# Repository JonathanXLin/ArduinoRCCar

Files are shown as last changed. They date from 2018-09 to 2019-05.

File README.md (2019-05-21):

# Wrist Controlled RC Car

This was a fun early project I made that let me consolidate my knowledge of C, Arduino electronics, and 3D modelling. I've included the Arduino code, prototype board schematics, and 3D models for the car and wrist controller.

<br>

<p align="center"> 
  
</p>

<p align="center"> 
  
</p>

<p align="center"> 
  
</p>

## Overview

The RC car uses two 12V geared DC motors, connected to a 2S Li-ion pack via a L293D dual H bridge. The H bridge is controlled by an Arduino Nano, which receives wireless commands from an NRF24L01 radio transceiver. 

The wrist controller consists of a GY-521 three-axis gyroscope module and an NRF24L01 radio transceiver controlled by an Arduino Nano. The controller is powered by a 9V battery.

<p align="center"> 
  
</p>

## Features

Once the car and wrist controller are powered on, the front lights will blink. When a connection is established (usually instant), the front lights will stay illuminated and the car will respond to the wrist controller. 

Holding the hand out parallel to the ground stops the car. Tilting the hand forward, back, left, and right drives the car in that respective direction. The car is capable of driving at a max forward speed of ~2 m/s, and can turn on a dime.

The car has a battery life of around 20 h of continuous heavy use.

## Code

All C code is original, except for the excellent TMRh20 library by Stefan Engelke for the NRF24L01 radio transceivers. 

## Schematics

The car and controller circuits were prototyped on breadboards before being built on two prototype boards. Fritzing was used to create digital schematics during this process.

## Models

The car shell and wheels were designed using SolidWorks and 3D printed using PLA filament. However, store bought wheels were used in the final design due to the need to superglue the 3D printed wheels (I might need to salvage the motors for later projects!)

## Photos

### Car Underside

<p align="center"> 
  
</p>

### Car and Controller Schematic Preview

<p align="center"> 
  
</p>

</br>

<p align="center"> 
  
</p>

### Prototypes

<p align="center"> 
  
</p>

</br>

<p align="center"> 
  
</p>

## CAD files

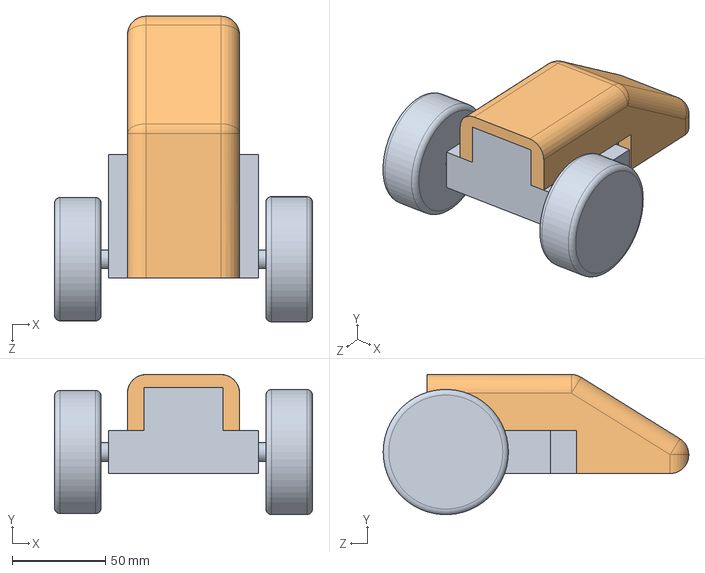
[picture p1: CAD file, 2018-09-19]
Models/V1 (Perfboard)/Car.SLDASM
138.0 x 74.9 x 163.5 mm
Internal Assembly

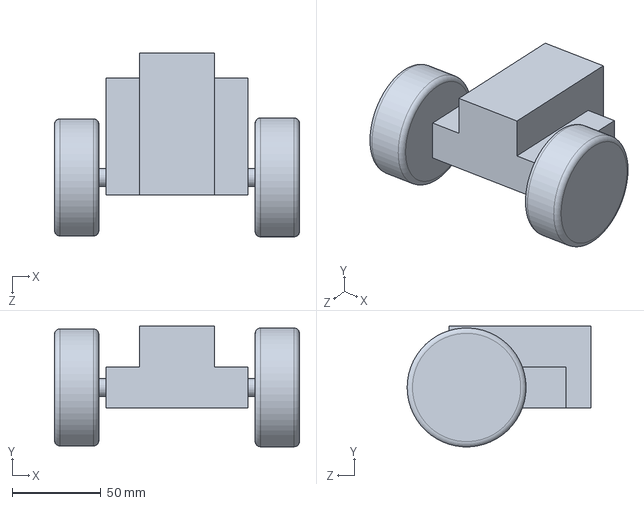
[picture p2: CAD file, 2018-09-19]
Models/V1 (Perfboard)/Internal Assembly.SLDPRT
138.0 x 67.9 x 103.5 mm

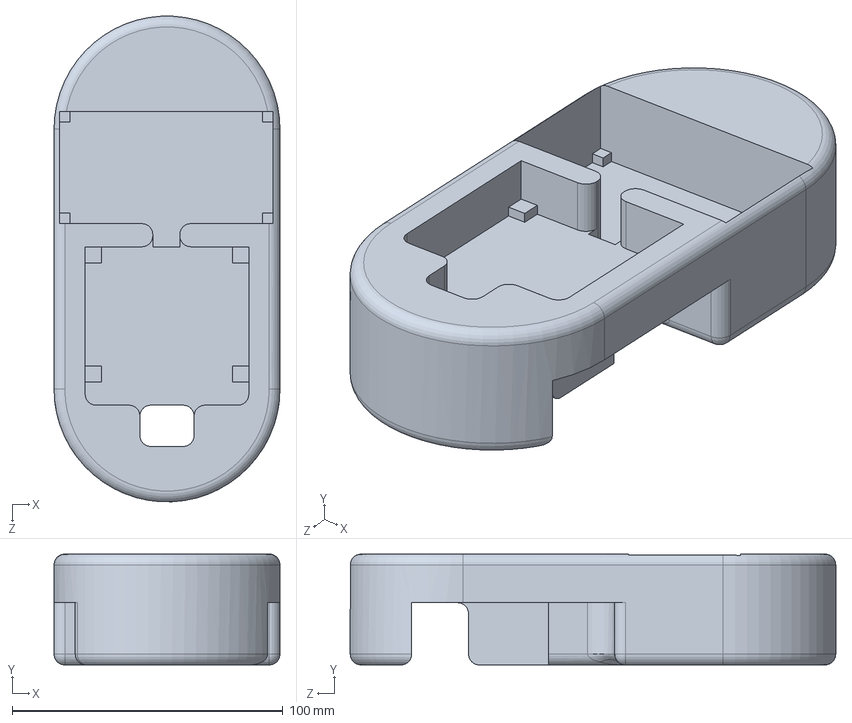
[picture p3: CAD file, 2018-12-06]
Models/V2 (PCB)/Car.SLDPRT
83.5 x 41.0 x 179.4 mm

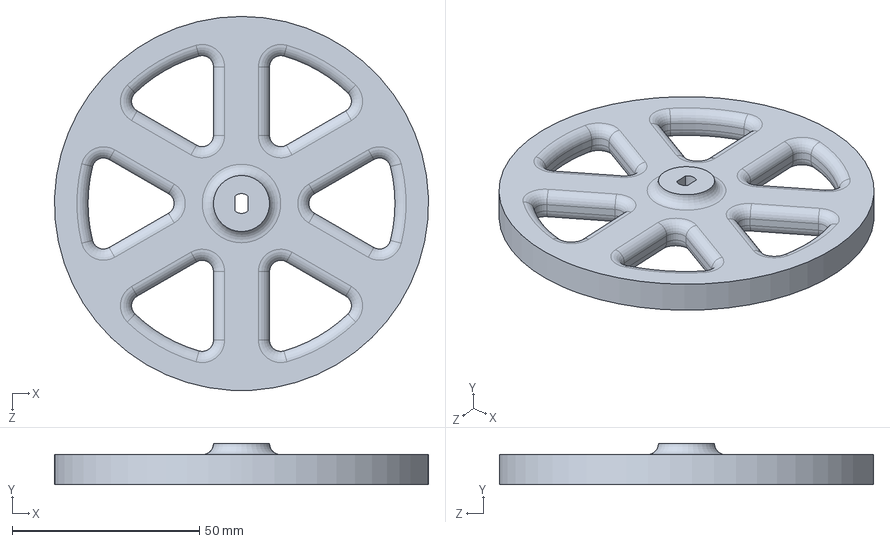
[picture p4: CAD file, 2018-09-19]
Models/V1 (Perfboard)/Traction Wheel.SLDPRT
100.0 x 11.0 x 100.0 mm

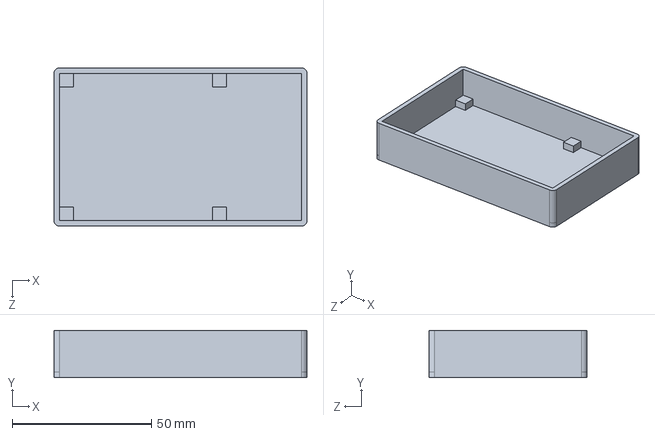
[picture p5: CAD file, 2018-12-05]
Models/V2 (PCB)/Controller (optional).SLDPRT
91.0 x 17.0 x 57.0 mm

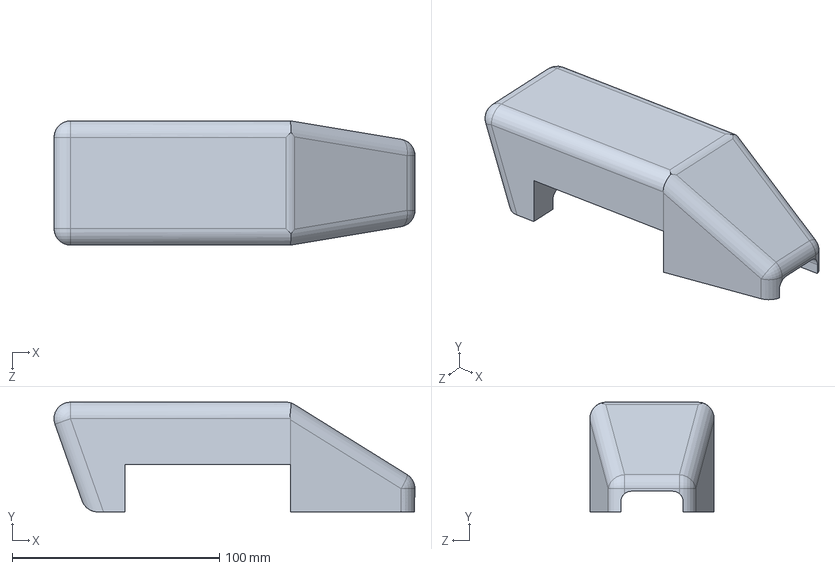
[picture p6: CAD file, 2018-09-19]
Models/V1 (Perfboard)/Shell.SLDPRT
174.2 x 53.0 x 60.0 mm

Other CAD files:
Models/V1 (Perfboard)/Shell.STL
Models/V2 (PCB)/Car.STL
Models/V2 (PCB)/Controller (optional).STL

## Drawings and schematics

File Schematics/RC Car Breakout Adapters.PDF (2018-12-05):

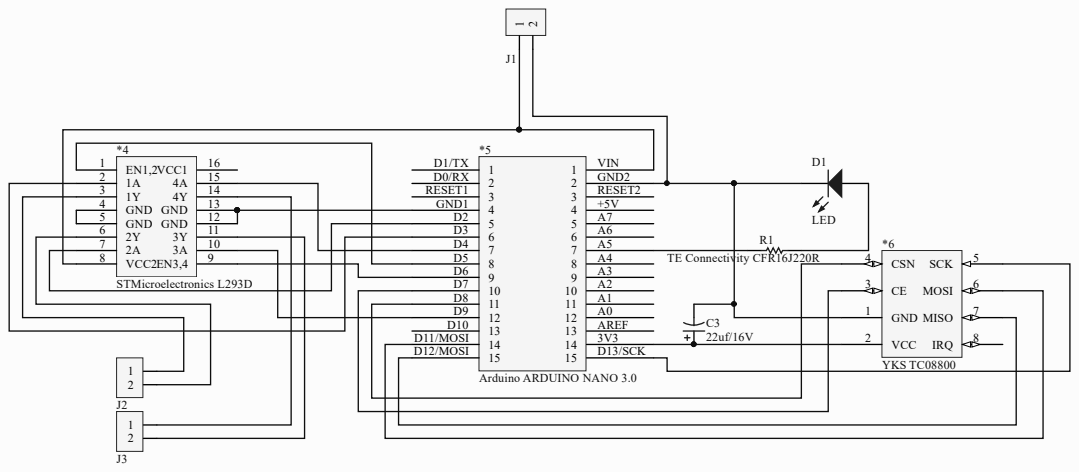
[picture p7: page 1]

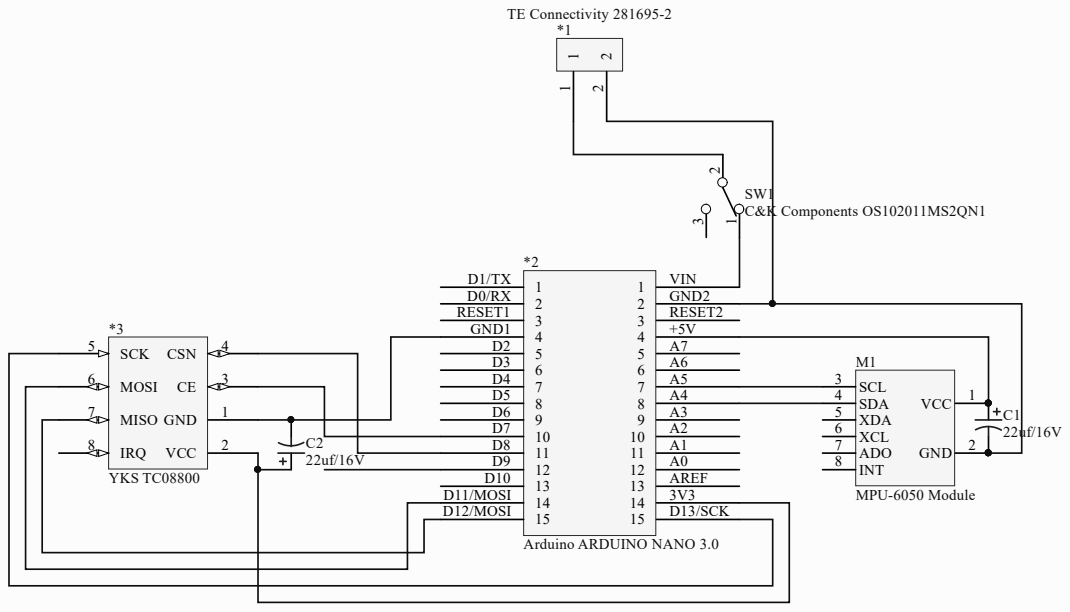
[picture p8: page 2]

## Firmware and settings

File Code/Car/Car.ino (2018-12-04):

#include <SPI.h>
#include "nRF24L01.h"
#include "RF24.h"

#include "Motor.h"

#define frontLED1   A5
#define frontLED2   A1

RF24 radio(7, 8);
//CE, CSN

const byte address[6] = "00001";

void setup() {
  
  radio.begin();
  radio.openReadingPipe(0, address);
  radio.setPALevel(RF24_PA_MAX);
  radio.setDataRate(RF24_250KBPS);
  radio.setChannel(115);
  radio.startListening();
  
  delay(200);

  Serial.begin(9600);
  Serial.println("Car Initialized");
  
  pinMode(ena, OUTPUT);
  pinMode(enb, OUTPUT);

  pinMode(in1, OUTPUT);
  pinMode(in2, OUTPUT);
  pinMode(in3, OUTPUT);
  pinMode(in4, OUTPUT);

  pinMode(frontLED1, OUTPUT);
  pinMode(frontLED2, OUTPUT);

  while (!radio.available())
  {
    front_light(150);
    delay(150);
  }

  front_light(1);
}

int ticksSinceLastConnection = 0;

int prevThrottle = 0;
int prevSteer = 0;

void loop() {

  read_and_drive();

  if (ticksSinceLastConnection >= 40)
  {
    prevThrottle = 0;
    prevSteer = 0;

    front_light(150);
    delay(150);
  }
  else
  {
    front_light(1);
  }

  delay(10);
}

bool isConnected = false;

void print_data()
{
  if (radio.available())
  {
    int package = -1;
    radio.read(&package, sizeof(int));
    
    int xState = package/100;
    int yState = package - xState*100;

    Serial.print("Package: ");
    Serial.print(package);
    Serial.print("\t");
    Serial.print("X: ");
    Serial.print(xState);
    Serial.print(" ");
    Serial.print("Y: ");
    Serial.print(yState);
    Serial.println();
  }
}

void read_data(int* xState, int* yState)
{
    int package = -1;
    radio.read(&package, sizeof(int));
    
    int x = package/100;
    int y = 0;
    
    if (x > 0)
      y = package - x*100 - 50;
    else
      y = package - x*100 + 50;

    if (x == 0)//Failed transmission, uses previous state
    {
      *xState = prevThrottle;
      *yState = prevSteer;

      ticksSinceLastConnection++;
    }
    else
    {
      if (x == 1)//Zero value transmitted
        *xState = 0;
      else//Nonzero value transmitted
        *xState = x;

      *yState = y*2;
        
      prevThrottle = *xState;
      prevSteer = *yState;

      Serial.print("Package: ");
      Serial.print(package);
      Serial.print("\t");
      Serial.print("X: ");
      Serial.print(*xState);
      Serial.print(" ");
      Serial.print("Y: ");
      Serial.print(*yState);
      Serial.println();

      ticksSinceLastConnection = 0;
    }
}

int xState = 0;
int yState = 0;

void read_and_drive()
{
  read_data(&xState, &yState);

  drive(xState + yState, xState - yState, 50);
}

void front_light(int dur)//if dur is 1, turns on, if dur is 0, turns off
{
  if (dur == 1)
  {
    digitalWrite(frontLED1, HIGH);
    digitalWrite(frontLED2, HIGH);
  }
  else if (dur == 0)
  {
    digitalWrite(frontLED1, LOW);
    digitalWrite(frontLED2, LOW);
  }
  else
  {
    digitalWrite(frontLED1, HIGH);
    digitalWrite(frontLED2, HIGH);
  
    delay(dur);
  
    digitalWrite(frontLED1, LOW);
    digitalWrite(frontLED2, LOW);
  }
}

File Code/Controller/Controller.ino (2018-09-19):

#include <SPI.h>
#include "nRF24L01.h"
#include "RF24.h"

#include "GY-521.h"

RF24 radio(7, 8);
//CE, CSN

const byte address[6] = "00001";

void setup() {
  setup_gyro();
  
  radio.begin();
  radio.openWritingPipe(address);
  radio.setPALevel(RF24_PA_MAX);
  radio.setDataRate(RF24_250KBPS);
  radio.setChannel(115);
  radio.stopListening();
  
  delay(200);

  Serial.begin(9600);
}

//Instantaneous -100 to 100 joystick positions
int xState = 0;
int yState = 0;

//All info sent via digits of package to radio
long package = 0;

void loop() {

  refresh_gyro();

  xState = map(angX, 0, 180, -99, 99);//Conversion from angles to state ranges
  yState = 99 - map(angY, 0, 180, 0, 99);

  if (xState>-15 && xState<15)//Range of values to trim to 0
    xState = 1;
  if (yState>40 && yState<60)
    yState = 50;

  if (xState>=0)//Converts states into package. Package is a 4 digit long integer, abcd, where ab is xState (-99 to 99), and cd is yState (0 to 99)
    package = xState * 100 + yState;
  else
    package = xState * 100 - yState;
      
  Serial.print(xState);
  Serial.print(" ");
  Serial.print(yState);
  Serial.print(" ");
  Serial.print(package);
  Serial.print(" ");
  Serial.println();

  radio.write(&package, sizeof(package));
  
  delay(100);
  
/*
    

    if (xState>0)//State represented by 4 digit long integer, abcd, where ab is xState (-99 to 99), and cd is yState (0 to 99)
      package = xState * 100 + yState + 50;
    else
      package = xState * 100 - yState + 50;
      
    Serial.println(package);

    radio.write(&package, sizeof(package));

    delay(10);

    */
}

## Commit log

2018-09-19 Added 3D Models and Schematics
    [Car Board.fzz, Car.SLDASM, Internal Assembly.SLDPRT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]
2018-09-19 Updated Schematics
    [Car Board.fzz, Controller Board.fzz]
2018-11-17 Breakout Adapter PCB
    Added Gerber files for PCB
    [PCB.GBL, PCB.GBO, PCB.GBP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]
2018-11-18 Edited Gerber files
    [Car.GBL, Car.GBO, Car.GBP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]
2018-11-21 Updated Gerber Files
    [Car.GBL, Car.GBO, Car.GBP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]
2018-12-04 Updated code to match PCB schematics
2018-12-05 Minor Tweaks
    [Car Board.fzz, Car.SLDASM, Car.SLDPRT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]
2018-12-06 Updated models to accomodate 2s 18650 holder
    [Car.SLDPRT, Car.STL]
2018-12-06 Minor tweaks to solidworks models
    [Controller (optional).SLDPRT, Controller (optional).STL]
